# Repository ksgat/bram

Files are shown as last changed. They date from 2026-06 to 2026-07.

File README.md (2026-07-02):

# BRAM!


BRAM is the underactuated, three legged, equilateral triangle from hell.

The project is mostly about control. BRAM’s motion is developed in MuJoCo first, where gait search and reinforcement
learning are used to discover usable crawling and turning behaviors. The current controller combines deterministic
forward/back gait patterns with learned yaw primitives, then blends them into joystick-style movement for the physical
robot.

Right now BRAM can crawl. The next major behavior is self-righting, so the robot can flip itself back over and continue
moving. The goal demo is a side-by-side comparison of the MuJoCo simulation and the real robot crawling, turning, and
eventually recovering from a flip.

## Demo

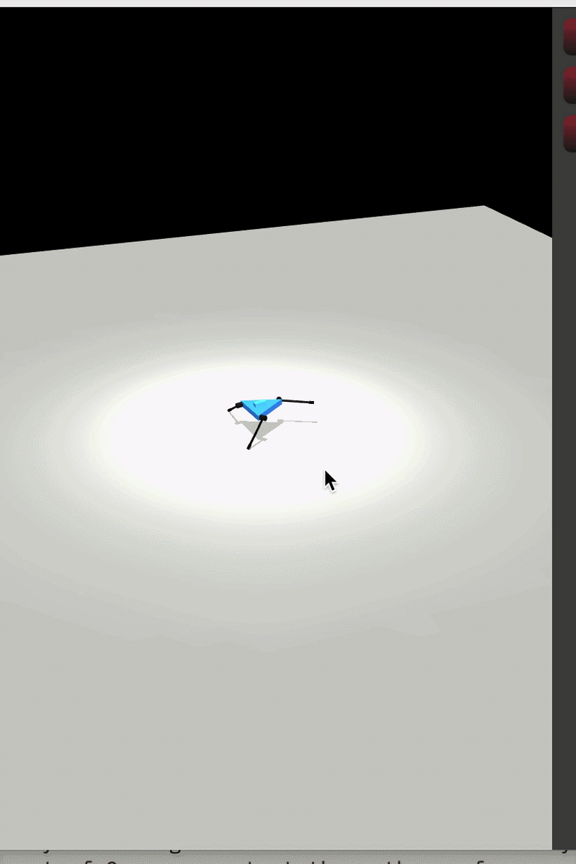
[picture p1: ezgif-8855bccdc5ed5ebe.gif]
BRAM crawling demo


## Project Structure

```text
BRAM
├── CAD/                  # STEP files for the full assembly and major mechanical parts
├── software/             # All robot software
│   ├── firmware/         # ESP32/XIAO firmware for the physical robot
│   └── gait_discovery/   # MuJoCo model, gait search, RL experiments, and controller exports
├── BOM.csv               # Bill of materials with parts, costs, and purchase links
├── JOURNAL.md            # High-level project journal and development summary
└── README.md             # Project overview, wiring notes, BOM table, and documentation
```

# Wiring diagram
Everything is handwired, no pcb.


## Bill of Materials

Source CSV: [BOM.csv](BOM.csv)

| Part | Quantity | Unit Cost | Total Cost | HC Cost | Link |
| --- | ---: | ---: | ---: | ---: | --- |
| 45 kg-cm servo | 3 | $24.99 | $74.97 | $74.97 | [Amazon](https://www.amazon.com/gp/product/B0CNFZ8BW8?smid=A28WSOZPYZ1XET&psc=1) |
| Xiao ESP32C3 | 1 | $10.99 | $10.99 | $10.99 | [Amazon](https://www.amazon.com/gp/product/B0DRNSV5CS?th=1) |
| 3/8 OD carbon rod | 1 | $7.73 | $7.73 | $0.00 | [Windcatcher RC](https://windcatcherrc.com/product/carbon-fiber-tube-10mm-x-8mm-x-1000mm/) |
| BEC | 1 | $8.99 | $8.99 | $8.99 | [Amazon](https://www.amazon.com/gp/product/B0DKTMGBHL?smid=A38CU2XC1RY0BO&psc=1) |
| 9DoF IMU | 1 | $20.49 | $20.49 | $20.49 | [Amazon](https://www.amazon.com/EC-Buying-Accelerometer-Gyroscope-Magnetometer/dp/B0CDGZMLPP) |
| M5 hardware | 1 | $9.99 | $9.99 | $9.99 | [Amazon](https://www.amazon.com/gp/product/B0FG2CT35D?th=1) |
| Ovionic 2S LiPo 1000 mAh | 1 | $23.99 | $23.99 | $23.99 | [Amazon](https://www.amazon.com/gp/product/B07CVBJ3SL?smid=A1KODDOPEPALCP&psc=1) |
| **Total** |  |  | **$157.15** | **$149.42** |  |

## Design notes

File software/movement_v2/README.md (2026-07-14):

# Movement V2

This folder is a BRAM-specific pass at the approach from Inoue et al.,
`Body Design and Gait Generation of Chair-Type Asymmetrical Tripedal Low-rigidity Robot`.

The important idea is not their exact servo angles. Their robot has six servos
and BRAM has three. The useful part to copy is the control structure:

- define a few essential postures
- linearly interpolate between them
- repeat those transitions for walking
- handle self-righting as a separate behavior
- use IMU orientation to decide when to enter or exit recovery

## What Their Repo Actually Has

- `connect_walk.py`: open-loop walking by repeated keyframe interpolation.
- `connect_stand.py` / `connect_once_stand.py`: keyframed stand-up motions.
- `rl_walk.py`: learned ONNX walking policy using IMU quaternion plus recent
  action history.
- `rl_stand.py`: learned ONNX stand-up policy using the same observation style.

They do not have joystick-style walking control. Their walking scripts are
forward-motion behaviors, not full directional teleop controllers.

## BRAM V2 Plan

For BRAM, the practical split should be:

- forward: one PPO-trained specialist primitive
- backward: one separate PPO-trained specialist primitive
- yaw: one PPO-trained yaw-only generalist conditioned on yaw command
- self-righting: separate keyframed recovery first, RL only after hardware
  keyframes exist
- mixed joystick arcs: disabled for demos unless the isolated primitives are
  visually reliable

This intentionally avoids one full joystick policy. Forward/back do not share a
command-conditioned policy, and yaw is the only generalist.

The file `bram_v2_keyframes.json` stores normalized servo commands in BRAM's
servo order:

```text
front, back_left, back_right
```

Values are normalized controller actions in `[-1, 1]`, not microseconds.

## Smoke Test

From the repo root:

```bash
python3 software/movement_v2/keyframe_controller.py \
  --sequence walk_forward \
  --steps 20
```

Backward has a separate seeded sequence:

```bash
python3 software/movement_v2/keyframe_controller.py \
  --sequence walk_backward \
  --steps 20
```

To export a longer command table:

```bash
python3 software/movement_v2/keyframe_controller.py \
  --sequence walk_forward \
  --cycles 10 \
  --csv /tmp/bram_walk_v2.csv
```

Run the MuJoCo primitive smoke suite:

```bash
python3 software/movement_v2/smoke_primitives.py --seconds 4
```

It reports forward/back distance, commanded yaw radians, drift, max tilt, min
chassis height, action delta RMS, and early termination for idle, random-small,
forward, backward, yaw `+1`, yaw `-1`, and half yaw commands.

## Primitive PPO

Use the V2 primitive PPO environment for all three base primitives. The reward
shape follows the paper's walking reward weights:

- progress: `30`
- chassis height: `20`
- upright seat: `5`
- heading/alignment: `2`
- alive: `1`
- death/reset: `-1`
- action delta: `-2`
- hinge velocity: `-2`

BRAM centers the height, upright, and heading/alignment terms at zero and adds a
small active-command stall penalty so standing still does not beat command
progress. The upright term is implemented as a tilt corridor: tilt up to about
`0.45 rad` is allowed because the 1-DOF legs need body rocking, then the penalty
ramps up through about `0.80 rad` and becomes harsher beyond that.

Forward/back specialists use a broad direction reward instead of exact
chassis-axis tracking. Net motion inside a `45 deg` cone gets full progress
credit and fades out by `65 deg`; path waste, wrong-way motion, yaw drift, and
excessive tilt are penalized separately. A slightly skewed but straight,
repeatable crawl is acceptable for the base primitive.

Policy observation:

- previous `4` IMU quaternion frames
- previous `6` normalized servo command frames
- yaw command scalar in `[-1, 1]` for yaw only; forward/back specialists receive
  `0`

Policy output:

- `3` normalized servo targets
- `20 Hz` by default with `--frame-skip 25`
- ESP32 runtime runs the actor online at `20 Hz` and sends normal `50 Hz` PWM
  pulses to the servos

Train the forward specialist:

```bash
.venv-rl/bin/python software/movement_v2/train_primitive_ppo.py \
  --primitive forward \
  --total-steps 300000 \
  --num-envs 4 \
  --episode-seconds 20 \
  --no-randomize-reset \
  --entropy-coef 0.0 \
  --log-std-init -0.8 \
  --hidden-size 128
```

Train the backward specialist separately:

```bash
.venv-rl/bin/python software/movement_v2/train_primitive_ppo.py \
  --primitive backward \
  --total-steps 200000 \
  --num-envs 4 \
  --episode-seconds 8
```

Train the yaw-only generalist:

```bash
.venv-rl/bin/python software/movement_v2/train_primitive_ppo.py \
  --primitive yaw \
  --total-steps 200000 \
  --num-envs 4 \
  --episode-seconds 8
```

Do not enable domain randomization until the nominal primitives move cleanly.
The trainer writes `policy.pt`, `policy_best.pt`, and `metrics.csv` under
`software/movement_v2/runs/rl_primitives/`.

Current corrected-geometry checkpoints use the `15.0 cm` leg endpoint in
`software/gait_discovery/bram.xml`:

- forward: `runs/rl_primitives/forward_primitive_20260706_173603/policy_best.pt`
- backward: `runs/rl_primitives/backward_primitive_20260706_173609/policy_best.pt`
- yaw: `runs/rl_primitives/yaw_primitive_20260706_174051/policy_best.pt`

The forward/back checkpoints are stable 20 second crawl primitives. A free PPO
fine-tune from those seeds was tested and rejected because deterministic eval
collapsed toward stationary behavior; keep the selected `policy_best.pt` files
unless a new run beats them in closed-loop smoke. Yaw was fine-tuned after the
leg-length change and selected with a balanced score over `-1`, `-0.5`, `0.5`,
and `1` yaw commands.

Yaw training now uses a stricter `gait_discovery`-style yaw-in-place eval:
signed yaw progress must be balanced against planar drift throughout the
rollout, action delta, action acceleration, roll/pitch rate, support loss,
contact slip, and chassis height warnings. The per-step yaw reward keeps the
paper's progress/height/up/action/velocity structure, but adds lighter versions
of those yaw-in-place terms so PPO sees the same failure modes without exploding
the value loss.

For the near-term hardware target, yaw drift is gated over time, not only at the
final pose. The current yaw gate is:

- final planar drift `<= 0.040 m`
- mean planar drift `<= 0.025 m`
- max planar drift `<= 0.040 m`
- no termination and no wrong-sign yaw

The base yaw controller should be searched before residual RL. Use the narrow
`yaw_low_drift` search space in `gait_discovery/search_gait.py`; it locks yaw
parameters that do not affect the open-loop CPG, keeps amplitudes/harmonics in a
smooth range, scores against a modest target yaw rate, and hard-gates final,
mean, and max path drift.

Run the base-search plus residual pipeline:

```bash
.venv-rl/bin/python software/movement_v2/run_yaw_base_residual_pipeline.py \
  --directions both \
  --iterations 24 \
  --population 96 \
  --episode-seconds-suite 4,8 \
  --frame-skip 50 \
  --output-hz 40 \
  --residual-steps 50000 \
  --no-randomize-reset
```

For a faster base-only pass:

```bash
.venv-rl/bin/python software/movement_v2/run_yaw_base_residual_pipeline.py \
  --directions both \
  --iterations 8 \
  --population 48 \
  --skip-residual
```

Residual yaw PPO lives in `train_yaw_residual_ppo.py`. It keeps the observation
block from the primitive policies, then appends fixed-base yaw features so the
residual can learn the base phase and timing. The base can be either a JSON
action table or the original searched CPG params; use params when table
resampling changes the contact timing.

- previous `4` IMU quaternion frames
- previous `6` emitted servo actions
- yaw command scalar
- current base action
- previous base action
- base phase `sin/cos`

The actor output is a residual, not a full servo command:

```text
final_action = base_yaw(t, yaw_cmd) + residual_limit * abs(yaw_cmd) * residual
```

Run a 50k residual cutoff test around explicit yaw tables:

```bash
.venv-rl/bin/python software/movement_v2/train_yaw_residual_ppo.py \
  --total-steps 50000 \
  --num-envs 4 \
  --rollout-steps 128 \
  --eval-interval 10 \
  --no-randomize-reset
```

The first 50k residual runs around the old 40 Hz planar yaw tables did **not**
meet the stricter gate. The best observed eval still had zero passing commands;
negative yaw drift stayed above `10 cm`. Treat this as a failed base/curriculum,
not a reason to train the same setup longer.

For a narrower right-yaw test, use direction-specific residual training with a
larger residual and a training-only drift curriculum:

```bash
.venv-rl/bin/python software/movement_v2/train_yaw_residual_ppo.py \
  --train-command yaw_neg1 \
  --eval-suite train \
  --total-steps 50000 \
  --num-envs 4 \
  --rollout-steps 128 \
  --eval-interval 10 \
  --no-randomize-reset \
  --residual-limit 0.35 \
  --start-final-drift-limit-m 0.12 \
  --start-mean-drift-limit-m 0.08 \
  --start-max-drift-limit-m 0.14 \
  --drift-curriculum-steps 50000
```

That run improved the `yaw_neg1` base from about `10.05 cm` final drift /
`13.58 cm` max drift to a best checkpoint around `6.59 cm` final drift /
`10.37 cm` max drift while keeping about `3.09 rad` yaw over `8 s`. It is a real
improvement, but still fails the current path-drift gate. The next thing to improve
is the right-yaw base primitive/search, not another broad residual PPO run.

Current final yaw candidate is packaged in
`software/movement_v2/exports/final_yaw_20260713/manifest.json`:

- full left yaw: `yaw-left_residual_policy_best.pt` on
  `yaw-left_base_params.json`, `2.285 rad`, `0.77 cm` final drift,
  `1.09 cm` mean drift, `1.97 cm` max drift, no termination. This runs at the
  searched CPG's native `10 Hz` hold timing.
- full right yaw: `yaw-right_residual_policy_finetuned_best.pt` on
  `yaw-right_residual_base_table.json`, `2.385 rad`, `0.53 cm` final drift,
  `1.07 cm` mean drift, `2.01 cm` max drift, no termination. This is the
  right-only fine-tuned checkpoint; the previous all-command-selected right
  checkpoint remains in the export package for comparison.
- direct left CPG fallback: `yaw-left_base_params.json`, `2.297 rad`,
  `2.70 cm` final drift, `1.11 cm` mean drift, `3.58 cm` max drift over `8 s`.
- the earlier all-direction residual policy is **not** a passing yaw generalist:
  `yaw_neg1` passed, but half-right and positive yaw did not. Use the
  direction-specific residual checkpoints for full left/right yaw.
- `yaw-left_base_table.json` is not promoted: interpolated table replay changes
  the 10 Hz held CPG contact timing and drifts heavily.

The old `gait_discovery` yaw tables are useful diagnostics, but they are not a
clean teacher on the corrected `15.0 cm` model: full negative yaw can flip sign
and full-rate tables drift heavily. Do not export a new yaw checkpoint unless it
beats the current strict eval and the visual smoke test.

Closed-loop checkpoint smoke test:

```bash
.venv-rl/bin/python software/movement_v2/smoke_policy_primitives.py --seconds 8
.venv-rl/bin/python software/movement_v2/smoke_policy_primitives.py --seconds 20
```

Visualize the same online policies in MuJoCo:

```bash
.venv-rl/bin/python software/movement_v2/visualize_policy_primitives.py --case suite --seconds 8
```

On macOS the script relaunches itself under `mjpython` when opening the viewer.
Use `--case forward`, `--case backward`, `--case yaw_pos`, or `--case yaw_neg`
to inspect one primitive at a time; add `--repeat` to keep looping.

Compare the current yaw actor against the saved degraded yaw actor:

```bash
.venv-rl/bin/python software/movement_v2/visualize_yaw_compare.py --case suite --seconds 8
```

Known corrected-geometry smoke results:

- `8s`: forward `0.1666 m`; backward broad-direction primary `0.0114 m`
  (`x=-0.068 m`, `y=0.125 m`); yaw `+1=2.378 rad`, `-1=1.054 rad`;
  no terminations.
- `20s`: forward `0.5151 m`; backward `0.3886 m`; yaw `+1=2.317 rad`,
  `-1=0.892 rad`; no terminations. Negative yaw drifts more than positive yaw.

## ESP32 Binding

The ESP32 runtime uses a hybrid primitive stack by default:

- forward/back run actor policies online
- yaw uses the base yaw table controller (`kUseBaseControllerForYaw = true`)
- firmware control tick is `25 ms`; yaw table output updates at that tick
- forward/back policy inference is held for two ticks, approximately `20 Hz`

This avoids promoting the 10 Hz yaw PPO fine-tune, which did not beat the
baseline strict eval. The online actor path still maintains the same observation
history as the MuJoCo env:

- previous `4` IMU quaternions, `wxyz`
- previous `6` emitted servo actions
- yaw command scalar for the yaw policy; `0` for forward/back

Export actor weights from the selected checkpoints:

```bash
.venv-rl/bin/python software/movement_v2/export_policy_header.py
```

This writes
`software/firmware/bram_esp32_controller/bram_policy_data.hpp`. The firmware
uses `bram_policy_controller.hpp` for tiny MLP inference and
`kUseOnlinePolicies = true` in
`software/firmware/bram_esp32_controller/bram_esp32_controller.ino`.
Yaw-only commands are routed through `bram_controller.hpp` while
`kUseBaseControllerForYaw` remains enabled.

Optional BNO08x IMU support is behind `BRAM_ENABLE_BNO08X_POLICY_IMU=1`. With
that flag enabled, the firmware reads the BNO080/BNO085 rotation vector as
`w,x,y,z` for the policy. Without it, the policy sees identity quaternion, which
is only useful for compile tests.

Then compile-check firmware:

```bash
arduino-cli compile --fqbn esp32:esp32:XIAO_ESP32C3 \
  software/firmware/bram_esp32_controller
```

## Runtime Arbitration

The ESP32 firmware maps joystick input to primitives with deadbands:

- left stick Y / `f` command: forward/back primitive
- right stick X / `y` command: yaw primitive
- both active: translation priority by default

Set `kBlendMixedCommands = true` in
`software/firmware/bram_esp32_controller/bram_esp32_controller.ino` only after
the isolated forward/back/yaw checks look clean.

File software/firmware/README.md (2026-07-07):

# Bram Firmware

The firmware runs movement_v2 actor policies online. It does not run MuJoCo,
PPO, or Python on-device; it runs exported tiny MLP actor weights from
`bram_esp32_controller/bram_policy_data.hpp` using the IMU quaternion and recent
servo-action history.

Movement V2 defaults to primitive arbitration for demos. If forward/back and yaw are both commanded at the same time, the sketch prioritizes translation and suppresses yaw. Set `kBlendMixedCommands = true` in `bram_esp32_controller/bram_esp32_controller.ino` only after the isolated primitives are reliable enough to re-enable mixed-arc blending.

## Layout

- `bram_esp32_controller/bram_esp32_controller.ino` is the Arduino sketch.
- `bram_esp32_controller/bram_controller.hpp` is the runtime controller logic.
- `bram_esp32_controller/bram_policy_controller.hpp` is the online actor runtime.
- `bram_esp32_controller/bram_policy_data.hpp` is generated actor weight data.
- `bram_esp32_controller/bram_controller_data.hpp` is generated fallback controller data.
- `bno08x_imu_test/bno08x_imu_test.ino` is a standalone BNO080/BNO085 IMU bring-up sketch for a XIAO ESP32-C3 with SDA on `D4` and SCL on `D5`.
- `tools/export_bram_firmware.py` regenerates the data header from a movement_v2 primitive bundle.

## Regenerate Policy Data

From the repo root:

```bash
.venv-rl/bin/python software/movement_v2/export_policy_header.py
```

`kUseOnlinePolicies = true` in the sketch selects this path. The older
`BramController` CPG/table path remains available as a fallback when
`kUseOnlinePolicies` is set to `false`.

## Arduino Dependencies

- ESP32 Arduino core.
- For the IMU test sketch, and for online policy IMU input when
  `BRAM_ENABLE_BNO08X_POLICY_IMU=1`: `Adafruit BNO08x` from Arduino Library Manager.

Native BLE command input is the default Arduino demo path:

```cpp
static constexpr bool kUseSerialInput = false;
```

The XIAO advertises as `BRAM` using a Nordic-UART-style BLE service:

- service UUID: `6e400001-b5a3-f393-e0a9-e50e24dcca9e`
- RX/write UUID: `6e400002-b5a3-f393-e0a9-e50e24dcca9e`
- TX/notify UUID: `6e400003-b5a3-f393-e0a9-e50e24dcca9e`

Send the same ASCII commands over BLE RX:

USB serial override is also enabled by default, so you can still send commands while BLE is compiled in:

```text
f 0.5 y -0.3
0.5 -0.3
stop
```

Set `kUseSerialInput = true` for serial-only bring-up.

The Bluepad32 gamepad hook is left behind `BRAM_ENABLE_BLUEPAD32`, but it is disabled by default. The Arduino Library Manager package named `Bluepad32 for NINA-W10 boards` is for NINA coprocessor boards and does not compile as native ESP32-C3 gamepad input.

## Compile Check

From the repo root:

```bash
arduino-cli compile --fqbn esp32:esp32:XIAO_ESP32C3 software/firmware/bram_esp32_controller
```

IMU test sketch:

```bash
arduino-cli compile --fqbn esp32:esp32:XIAO_ESP32C3 software/firmware/bno08x_imu_test
```

## Safety Notes

- Power servos directly from the 2S battery only if the servos are rated for `8.4 V`.
- Power the ESP32/control electronics from the BEC/regulator, not from the servo rail unless the board regulator supports it.
- Tie battery ground, servo ground, BEC ground, and ESP32 ground together.
- Start with conservative servo pulse limits in the sketch before testing on the robot.
- Bench test with servos disconnected from the mechanism first.

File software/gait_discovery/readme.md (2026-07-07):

3 legged robo

## Setup

```bash
python3 -m venv .venv
source .venv/bin/activate
python -m pip install --upgrade pip
python -m pip install -e .
```

PufferLib currently depends on Torch. If Torch has a wheel for your `python3`,
install the RL stack with:

```bash
python -m pip install -e ".[rl]"
```

For the working RL setup in this directory, use the Python 3.12 venv:

```bash
source .venv-rl/bin/activate
python puffer_smoke.py
```

## Run

Smoke-test the MuJoCo model without opening a window:

```bash
python main.py --headless --seconds 3
```

Open the interactive viewer frozen so you can inspect and tweak the model:

```bash
.venv/bin/mjpython main.py --seconds 0 --pause
```

Run the interactive viewer with a simple sinusoidal starter gait:

```bash
.venv/bin/mjpython main.py
```

Check the Gymnasium environment scaffold that PufferLib can wrap later:

```bash
python main.py --env-check --seconds 3
```

## Movement V2 Training

The current control direction is under `software/movement_v2`: separate
forward/back RL specialist primitives plus a yaw-only command-conditioned RL
generalist. Do not train the old full joystick PPO policy for the base demo.

Train each primitive from the repo root:

```bash
.venv-rl/bin/python software/movement_v2/train_primitive_ppo.py \
  --primitive forward \
  --total-steps 200000 \
  --num-envs 4

.venv-rl/bin/python software/movement_v2/train_primitive_ppo.py \
  --primitive backward \
  --total-steps 200000 \
  --num-envs 4

.venv-rl/bin/python software/movement_v2/train_primitive_ppo.py \
  --primitive yaw \
  --total-steps 200000 \
  --num-envs 4
```

Smoke-test the current primitive controller from the repo root:

```bash
python3 software/movement_v2/smoke_primitives.py --seconds 4
```

The older CAD-mesh attempt is saved as `bram_cad_attempt.xml`. The active
`bram.xml` is a measured hand-written model with a 7.5 inch equilateral
triangle chassis and primitive servo/leg bodies for simulation and RL.

On macOS, MuJoCo's viewer should be launched with:

```bash
.venv/bin/mjpython main.py
```

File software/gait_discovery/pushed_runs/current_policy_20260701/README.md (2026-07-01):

# Bram Current Policy Package - 2026-07-01

This folder is the compact policy snapshot to share/push.

## Reviewable Controller

Current usable policy is the exact component controller:

- forward: deterministic CPG gait in `gaits/forward_best_params.json`
- backward: deterministic CPG gait in `gaits/backward_best_params.json`
- left yaw: exported PPO action table in `yaw_tables/yaw_left_policy_table.json`
- right yaw: exported PPO action table in `yaw_tables/yaw_right_policy_table.json`

Visual review command from repo root:

```bash
.venv-rl/bin/mjpython train_cpg_modulator.py \
  --teacher-controller \
  --forward-gait pushed_runs/current_policy_20260701/gaits/forward_best_params.json \
  --backward-gait pushed_runs/current_policy_20260701/gaits/backward_best_params.json \
  --yaw-left-table pushed_runs/current_policy_20260701/yaw_tables/yaw_left_policy_table.json \
  --yaw-right-table pushed_runs/current_policy_20260701/yaw_tables/yaw_right_policy_table.json \
  --view \
  --view-command primitives \
  --speed 0.8
```

Headless check:

```bash
.venv-rl/bin/python -u train_cpg_modulator.py \
  --teacher-controller \
  --forward-gait pushed_runs/current_policy_20260701/gaits/forward_best_params.json \
  --backward-gait pushed_runs/current_policy_20260701/gaits/backward_best_params.json \
  --yaw-left-table pushed_runs/current_policy_20260701/yaw_tables/yaw_left_policy_table.json \
  --yaw-right-table pushed_runs/current_policy_20260701/yaw_tables/yaw_right_policy_table.json \
  --eval-episodes 1
```

## Status

Primitive commands are reviewable: idle, forward, backward, left yaw, right yaw.

Mixed forward+yaw arcs are not final. Naive blending can terminate or underperform, so do not present that as solved Xbox control yet.

The learned CPG-modulator checkpoint in `experimental_cpg_modulator/` is preserved for reference, but it is not the current best visual policy because it loses too much left-yaw authority.

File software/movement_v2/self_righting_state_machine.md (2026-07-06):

# Self-Righting State Machine Sketch

This is the movement-v2 equivalent of the paper's stand-up split.

The paper's useful pattern:

1. Use IMU quaternion to estimate whether the body is down or upright.
2. If down, run a recovery behavior.
3. If the seat/body becomes upright enough, transition to a normal standing
   posture.
4. Keep stand-up separate from walking.

For BRAM:

```text
state = upright

if up_projection < fallen_threshold:
    state = fallen

fallen:
    choose recovery sequence based on roll/pitch quadrant
    play keyframed kick sequence
    if up_projection > recovered_threshold:
        state = recover_to_neutral

recover_to_neutral:
    interpolate current servo commands to neutral
    state = upright
```

The first real hardware task is not RL. It is to discover three or four
`self_right_*` keyframe sequences by testing the physical robot:

- fallen on left side
- fallen on right side
- upside down / battery-side-up safe case
- awkward partial side case

Once those work manually, an RL policy can be trained around those same motion
families instead of searching from nothing.

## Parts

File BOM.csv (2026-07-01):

Part | Quantity | Unit Cost | Total Cost | HC cost | Links
45 kg-cm servo | 3 | 24.99 | 74.97 | 74.97 | https://www.amazon.com/gp/product/B0CNFZ8BW8?smid=A28WSOZPYZ1XET&psc=1
Xiao ESP32c3 | 1 | 10.99 | 10.99 | 10.99 | https://www.amazon.com/gp/product/B0DRNSV5CS?th=1
3/8 od carbon rod | 1 | 7.73 | 7.73 | 0 | https://windcatcherrc.com/product/carbon-fiber-tube-10mm-x-8mm-x-1000mm/
BEC | 1 | 8.99 | 8.99 | 8.99 | https://www.amazon.com/gp/product/B0DKTMGBHL?smid=A38CU2XC1RY0BO&psc=1
9dof IMU | 1 | 20.49 | 20.49 | 20.49 | https://www.amazon.com/EC-Buying-Accelerometer-Gyroscope-Magnetometer/dp/B0CDGZMLPP
M5 Hardware | 1 | 9.99 | 9.99 | 9.99 | https://www.amazon.com/gp/product/B0FG2CT35D?th=1
Ovionic 2s lipo 1000mah | 1 | 23.99 | 23.99 | 23.99 | https://www.amazon.com/gp/product/B07CVBJ3SL?smid=A1KODDOPEPALCP&psc=1
 |  |  |  | 149.42

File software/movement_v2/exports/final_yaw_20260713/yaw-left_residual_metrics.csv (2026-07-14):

update | global_step | sps | recent_return | recent_yaw | recent_length | eval_reward | eval_score | eval_yaw_distance | eval_planar_drift | eval_mean_planar_drift | eval_max_planar_drift | eval_pass_count | eval_length | policy_loss | value_loss | entropy | approx_kl | yaw_neg1_score | yaw_neg1_yaw_distance | yaw_neg1_target_yaw_distance | yaw_neg1_planar_drift | yaw_neg1_mean_planar_drift | yaw_neg1_max_planar_drift | yaw_neg1_pass_gate | yaw_neg1_length | yaw_neg1_terminated | yaw_neg05_score | yaw_neg05_yaw_distance | yaw_neg05_target_yaw_distance | yaw_neg05_planar_drift | yaw_neg05_mean_planar_drift | yaw_neg05_max_planar_drift | yaw_neg05_pass_gate | yaw_neg05_length | yaw_neg05_terminated | yaw_pos05_score | yaw_pos05_yaw_distance | yaw_pos05_target_yaw_distance | yaw_pos05_planar_drift | yaw_pos05_mean_planar_drift | yaw_pos05_max_planar_drift | yaw_pos05_pass_gate | yaw_pos05_length | yaw_pos05_terminated | yaw_pos1_score | yaw_pos1_yaw_distance | yaw_pos1_target_yaw_distance | yaw_pos1_planar_drift | yaw_pos1_mean_planar_drift | yaw_pos1_max_planar_drift | yaw_pos1_pass_gate | yaw_pos1_length | yaw_pos1_terminated
0 | 0 | 0 | nan | nan | nan | -78.09704811332792 | 8.875966993203743 | 2.297307244669511 | 0.026965498014792772 | 0.011092310719643832 | 0.03581876571649391 | 1 | 80.0 | nan | nan | nan | nan | nan | nan | nan | nan | nan | nan | 0 | 0 | 0 | nan | nan | nan | nan | nan | nan | 0 | 0 | 0 | nan | nan | nan | nan | nan | nan | 0 | 0 | 0 | 8.875966993203743 | 2.297307244669511 | 2.88 | 0.026965498014792772 | 0.011092310719643832 | 0.03581876571649391 | 1 | 80 | 0
1 | 512 | 113 | -215.59188842773438 | 2.056629925966263 | 80.0 | -91.17165140857401 | 8.863121116751898 | 2.276606192984462 | 0.021429484376861468 | 0.01207449133161769 | 0.03288986284346611 | 1 | 80.0 | -0.006232545245438814 | 1188.658447265625 | -1.7429437190294266 | 0.0023840881476644427 | nan | nan | nan | nan | nan | nan | 0 | 0 | 0 | nan | nan | nan | nan | nan | nan | 0 | 0 | 0 | nan | nan | nan | nan | nan | nan | 0 | 0 | 0 | 8.863121116751898 | 2.276606192984462 | 2.88 | 0.021429484376861468 | 0.01207449133161769 | 0.03288986284346611 | 1 | 80 | 0
2 | 1024 | 161 | -285.87597783406574 | 2.0912417074044547 | 80.0 | -125.88445402428233 | 8.490456065211763 | 2.240928957060979 | 0.024670390820816727 | 0.014803712086656567 | 0.03478927111857449 | 1 | 80.0 | -0.0021831186022609472 | 1443.1299743652344 | -1.7423519790172577 | 0.0005918559618294239 | nan | nan | nan | nan | nan | nan | 0 | 0 | 0 | nan | nan | nan | nan | nan | nan | 0 | 0 | 0 | nan | nan | nan | nan | nan | nan | 0 | 0 | 0 | 8.490456065211763 | 2.240928957060979 | 2.88 | 0.024670390820816727 | 0.014803712086656567 | 0.03478927111857449 | 1 | 80 | 0
3 | 1536 | 134 | -268.3898801803589 | 2.095084436237812 | 80.0 | nan | nan | nan | nan | nan | nan | 0 | nan | -9.35759162530303e-05 | 1222.3472137451172 | -1.741686835885048 | 0.000198695546714589 | nan | nan | nan | nan | nan | nan | 0 | 0 | 0 | nan | nan | nan | nan | nan | nan | 0 | 0 | 0 | nan | nan | nan | nan | nan | nan | 0 | 0 | 0 | nan | nan | nan | nan | nan | nan | 0 | 0 | 0
4 | 2048 | 134 | -288.5811055501302 | 2.1124853640794754 | 80.0 | -120.41276054254166 | 4.610916729292138 | 2.3164589277245926 | 0.034980793053208704 | 0.014679767721581827 | 0.044401490344556864 | 0 | 80.0 | -0.00024643843062222004 | 1690.8291778564453 | -1.7414662688970566 | 0.0001916783512569964 | nan | nan | nan | nan | nan | nan | 0 | 0 | 0 | nan | nan | nan | nan | nan | nan | 0 | 0 | 0 | nan | nan | nan | nan | nan | nan | 0 | 0 | 0 | 7.110916729292138 | 2.3164589277245926 | 2.88 | 0.034980793053208704 | 0.014679767721581827 | 0.044401490344556864 | 0 | 80 | 0
5 | 2560 | 149 | -306.94011783599854 | 2.1327952332794666 | 80.0 | nan | nan | nan | nan | nan | nan | 0 | nan | -0.0007851677946746349 | 3420.993438720703 | -1.741483435034752 | 0.000170806422829628 | nan | nan | nan | nan | nan | nan | 0 | 0 | 0 | nan | nan | nan | nan | nan | nan | 0 | 0 | 0 | nan | nan | nan | nan | nan | nan | 0 | 0 | 0 | nan | nan | nan | nan | nan | nan | 0 | 0 | 0
6 | 3072 | 160 | -322.43120744493274 | 2.13493569360839 | 80.0 | -120.43987456281248 | 4.6526114084536765 | 2.3044611638456294 | 0.033731278076758624 | 0.015074912489035835 | 0.04409164144750158 | 0 | 80.0 | -0.0005377861671149731 | 3846.479705810547 | -1.741939589381218 | 0.00018876910326071084 | nan | nan | nan | nan | nan | nan | 0 | 0 | 0 | nan | nan | nan | nan | nan | nan | 0 | 0 | 0 | nan | nan | nan | nan | nan | nan | 0 | 0 | 0 | 7.1526114084536765 | 2.3044611638456294 | 2.88 | 0.033731278076758624 | 0.015074912489035835 | 0.04409164144750158 | 0 | 80 | 0
7 | 3584 | 171 | -322.57157412442297 | 2.132972080599178 | 80.0 | nan | nan | nan | nan | nan | nan | 0 | nan | -0.0012405018787831068 | 1769.1678771972656 | -1.7423667907714844 | 0.00019739862182177603 | nan | nan | nan | nan | nan | nan | 0 | 0 | 0 | nan | nan | nan | nan | nan | nan | 0 | 0 | 0 | nan | nan | nan | nan | nan | nan | 0 | 0 | 0 | nan | nan | nan | nan | nan | nan | 0 | 0 | 0
8 | 4096 | 178 | -320.8567132949829 | 2.1462789848446846 | 80.0 | -107.68187977309302 | 8.936505464135385 | 2.291422643907503 | 0.021455192231240993 | 0.0137942464306352 | 0.03228293064448837 | 1 | 80.0 | -0.0022577412892132998 | 1843.5677947998047 | -1.7425979971885681 | 0.00041416112799197435 | nan | nan | nan | nan | nan | nan | 0 | 0 | 0 | nan | nan | nan | nan | nan | nan | 0 | 0 | 0 | nan | nan | nan | nan | nan | nan | 0 | 0 | 0 | 8.936505464135385 | 2.291422643907503 | 2.88 | 0.021455192231240993 | 0.0137942464306352 | 0.03228293064448837 | 1 | 80 | 0
9 | 4608 | 187 | -319.1342626953125 | 2.155916862487793 | 80.0 | nan | nan | nan | nan | nan | nan | 0 | nan | -0.0013407910009846091 | 761.0855102539062 | -1.7427754998207092 | 0.0008012168982531875 | nan | nan | nan | nan | nan | nan | 0 | 0 | 0 | nan | nan | nan | nan | nan | nan | 0 | 0 | 0 | nan | nan | nan | nan | nan | nan | 0 | 0 | 0 | nan | nan | nan | nan | nan | nan | 0 | 0 | 0
10 | 5120 | 188 | -320.43579467773435 | 2.165974678993225 | 80.0 | -100.35265956054639 | 8.82886450821495 | 2.282308852580516 | 0.020614072309987307 | 0.014099430399416264 | 0.034358447084476905 | 1 | 80.0 | -0.002434961381368339 | 2156.197952270508 | -1.7430506199598312 | 0.0007484124216716737 | nan | nan | nan | nan | nan | nan | 0 | 0 | 0 | nan | nan | nan | nan | nan | nan | 0 | 0 | 0 | nan | nan | nan | nan | nan | nan | 0 | 0 | 0 | 8.82886450821495 | 2.282308852580516 | 2.88 | 0.020614072309987307 | 0.014099430399416264 | 0.034358447084476905 | 1 | 80 | 0
11 | 5632 | 191 | -323.9023434448242 | 2.1666896677017213 | 80.0 | nan | nan | nan | nan | nan | nan | 0 | nan | -0.0023284878116101027 | 952.2683639526367 | -1.743542656302452 | 0.000801826681708917 | nan | nan | nan | nan | nan | nan | 0 | 0 | 0 | nan | nan | nan | nan | nan | nan | 0 | 0 | 0 | nan | nan | nan | nan | nan | nan | 0 | 0 | 0 | nan | nan | nan | nan | nan | nan | 0 | 0 | 0
12 | 6144 | 195 | -295.5328497314453 | 2.1804311943054198 | 80.0 | -87.12478005640234 | 9.339613329288838 | 2.298017162767352 | 0.012128765080281814 | 0.011662179508494573 | 0.024179323276664864 | 1 | 80.0 | -0.0023581632412970066 | 1116.783935546875 | -1.7444330900907516 | 0.0009100497118197381 | nan | nan | nan | nan | nan | nan | 0 | 0 | 0 | nan | nan | nan | nan | nan | nan | 0 | 0 | 0 | nan | nan | nan | nan | nan | nan | 0 | 0 | 0 | 9.339613329288838 | 2.298017162767352 | 2.88 | 0.012128765080281814 | 0.011662179508494573 | 0.024179323276664864 | 1 | 80 | 0
13 | 6656 | 200 | -289.9158367919922 | 2.1742055225372314 | 80.0 | nan | nan | nan | nan | nan | nan | 0 | nan | -0.0040024431655183434 | 1420.642105102539 | -1.7449567466974258 | 0.0011736343149095774 | nan | nan | nan | nan | nan | nan | 0 | 0 | 0 | nan | nan | nan | nan | nan | nan | 0 | 0 | 0 | nan | nan | nan | nan | nan | nan | 0 | 0 | 0 | nan | nan | nan | nan | nan | nan | 0 | 0 | 0
14 | 7168 | 203 | -276.1464279174805 | 2.1651543283462527 | 80.0 | -79.63193378074345 | 9.437222324726761 | 2.2849689903253645 | 0.007728018303852137 | 0.010865370187007672 | 0.01974429430775138 | 1 | 80.0 | -0.0002615319099277258 | 1067.052719116211 | -1.74544657766819 | 0.0008116946555674076 | nan | nan | nan | nan | nan | nan | 0 | 0 | 0 | nan | nan | nan | nan | nan | nan | 0 | 0 | 0 | nan | nan | nan | nan | nan | nan | 0 | 0 | 0 | 9.437222324726761 | 2.2849689903253645 | 2.88 | 0.007728018303852137 | 0.010865370187007672 | 0.01974429430775138 | 1 | 80 | 0
15 | 7680 | 207 | -266.9028775024414 | 2.1699917030334475 | 80.0 | nan | nan | nan | nan | nan | nan | 0 | nan | -0.0010701597202569246 | 1390.4797668457031 | -1.7461276352405548 | 0.00024437750107608736 | nan | nan | nan | nan | nan | nan | 0 | 0 | 0 | nan | nan | nan | nan | nan | nan | 0 | 0 | 0 | nan | nan | nan | nan | nan | nan | 0 | 0 | 0 | nan | nan | nan | nan | nan | nan | 0 | 0 | 0
16 | 8192 | 209 | -267.7662631225586 | 2.1632811880111693 | 80.0 | -103.10875929601954 | 8.806874486102613 | 2.2723394857220907 | 0.024403300441146022 | 0.012087439635926997 | 0.032330651847572535 | 1 | 80.0 | -0.0021599638275802135 | 2004.5359954833984 | -1.7467014789581299 | 0.0008250415557995439 | nan | nan | nan | nan | nan | nan | 0 | 0 | 0 | nan | nan | nan | nan | nan | nan | 0 | 0 | 0 | nan | nan | nan | nan | nan | nan | 0 | 0 | 0 | 8.806874486102613 | 2.2723394857220907 | 2.88 | 0.024403300441146022 | 0.012087439635926997 | 0.032330651847572535 | 1 | 80 | 0
17 | 8704 | 212 | -276.6772448730469 | 2.1660648727416993 | 80.0 | nan | nan | nan | nan | nan | nan | 0 | nan | -0.0030118994181975722 | 1510.5919799804688 | -1.7471470087766647 | 0.0005944909353274852 | nan | nan | nan | nan | nan | nan | 0 | 0 | 0 | nan | nan | nan | nan | nan | nan | 0 | 0 | 0 | nan | nan | nan | nan | nan | nan | 0 | 0 | 0 | nan | nan | nan | nan | nan | nan | 0 | 0 | 0
18 | 9216 | 213 | -269.59364227294924 | 2.157653431892395 | 80.0 | -127.00554058545762 | 8.760962868283372 | 2.28613380883249 | 0.023988046942711602 | 0.01556951472531741 | 0.035325073140174704 | 1 | 80.0 | -0.0015092790126800537 | 818.7760696411133 | -1.7476044595241547 | 0.00042966686305589974 | nan | nan | nan | nan | nan | nan | 0 | 0 | 0 | nan | nan | nan | nan | nan | nan | 0 | 0 | 0 | nan | nan | nan | nan | nan | nan | 0 | 0 | 0 | 8.760962868283372 | 2.28613380883249 | 2.88 | 0.023988046942711602 | 0.01556951472531741 | 0.035325073140174704 | 1 | 80 | 0
19 | 9728 | 217 | -271.63132629394534 | 2.137074987888336 | 80.0 | nan | nan | nan | nan | nan | nan | 0 | nan | -0.002291706157848239 | 987.0267791748047 | -1.7480761408805847 | 0.0008038238156586885 | nan | nan | nan | nan | nan | nan | 0 | 0 | 0 | nan | nan | nan | nan | nan | nan | 0 | 0 | 0 | nan | nan | nan | nan | nan | nan | 0 | 0 | 0 | nan | nan | nan | nan | nan | nan | 0 | 0 | 0
20 | 10240 | 220 | -272.75359924316405 | 2.1426914167404174 | 80.0 | -166.90979273405935 | 4.695495915324231 | 2.267954185433557 | 0.030283947652945165 | 0.020874085179074527 | 0.04314799024079253 | 0 | 80.0 | -0.0012540662719402462 | 1540.7567901611328 | -1.7483916133642197 | 0.000889971706783399 | nan | nan | nan | nan | nan | nan | 0 | 0 | 0 | nan | nan | nan | nan | nan | nan | 0 | 0 | 0 | nan | nan | nan | nan | nan | nan | 0 | 0 | 0 | 7.195495915324231 | 2.267954185433557 | 2.88 | 0.030283947652945165 | 0.020874085179074527 | 0.04314799024079253 | 0 | 80 | 0
21 | 10752 | 225 | -263.28797821044924 | 2.1421982717514036 | 80.0 | nan | nan | nan | nan | nan | nan | 0 | nan | -0.0015402310527861118 | 645.6778259277344 | -1.74872887134552 | 0.00040574491140432656 | nan | nan | nan | nan | nan | nan | 0 | 0 | 0 | nan | nan | nan | nan | nan | nan | 0 | 0 | 0 | nan | nan | nan | nan | nan | nan | 0 | 0 | 0 | nan | nan | nan | nan | nan | nan | 0 | 0 | 0
22 | 11264 | 227 | -262.37170562744143 | 2.143997001647949 | 80.0 | -96.4414676599093 | 8.404166073944149 | 2.2316835611774364 | 0.028872601691001674 | 0.01225708752521146 | 0.03527384658654585 | 1 | 80.0 | -0.0011414227774366736 | 929.2920303344727 | -1.7488564997911453 | 0.0004748171486426145 | nan | nan | nan | nan | nan | nan | 0 | 0 | 0 | nan | nan | nan | nan | nan | nan | 0 | 0 | 0 | nan | nan | nan | nan | nan | nan | 0 | 0 | 0 | 8.404166073944149 | 2.2316835611774364 | 2.88 | 0.028872601691001674 | 0.01225708752521146 | 0.03527384658654585 | 1 | 80 | 0
23 | 11776 | 231 | -271.01082427978514 | 2.1241167688369753 | 80.0 | nan | nan | nan | nan | nan | nan | 0 | nan | -0.0009474039543420076 | 2235.292022705078 | -1.7487842738628387 | 0.0005351805011741817 | nan | nan | nan | nan | nan | nan | 0 | 0 | 0 | nan | nan | nan | nan | nan | nan | 0 | 0 | 0 | nan | nan | nan | nan | nan | nan | 0 | 0 | 0 | nan | nan | nan | nan | nan | nan | 0 | 0 | 0
24 | 12288 | 233 | -258.1648049926758 | 2.1325091195106505 | 80.0 | -79.47524758470921 | 8.767814654925802 | 2.231439030125139 | 0.01983497332444898 | 0.009603146122758123 | 0.02708923793598895 | 1 | 80.0 | -0.0014599787537008524 | 444.45567321777344 | -1.7484618872404099 | 0.0004370755923446268 | nan | nan | nan | nan | nan | nan | 0 | 0 | 0 | nan | nan | nan | nan | nan | nan | 0 | 0 | 0 | nan | nan | nan | nan | nan | nan | 0 | 0 | 0 | 8.767814654925802 | 2.231439030125139 | 2.88 | 0.01983497332444898 | 0.009603146122758123 | 0.02708923793598895 | 1 | 80 | 0
25 | 12800 | 236 | -245.10702392578125 | 2.1343492388725283 | 80.0 | nan | nan | nan | nan | nan | nan | 0 | nan | -0.0021292422607075423 | 920.6499633789062 | -1.748024806380272 | 0.0008261803886853158 | nan | nan | nan | nan | nan | nan | 0 | 0 | 0 | nan | nan | nan | nan | nan | nan | 0 | 0 | 0 | nan | nan | nan | nan | nan | nan | 0 | 0 | 0 | nan | nan | nan | nan | nan | nan | 0 | 0 | 0
26 | 13312 | 238 | -254.84767791748047 | 2.139894070625305 | 80.0 | -87.99239714802808 | 8.466185835168282 | 2.210131020510794 | 0.02288907187016557 | 0.010233567177305787 | 0.03150732454617612 | 1 | 80.0 | -0.00014421611558645964 | 2069.5587005615234 | -1.7479811310768127 | 0.000597219419432804 | nan | nan | nan | nan | nan | nan | 0 | 0 | 0 | nan | nan | nan | nan | nan | nan | 0 | 0 | 0 | nan | nan | nan | nan | nan | nan | 0 | 0 | 0 | 8.466185835168282 | 2.210131020510794 | 2.88 | 0.02288907187016557 | 0.010233567177305787 | 0.03150732454617612 | 1 | 80 | 0
27 | 13824 | 241 | -261.53398193359374 | 2.141196961402893 | 80.0 | nan | nan | nan | nan | nan | nan | 0 | nan | -0.0022259445395320654 | 1460.4608459472656 | -1.7481644749641418 | 0.0002528903423808515 | nan | nan | nan | nan | nan | nan | 0 | 0 | 0 | nan | nan | nan | nan | nan | nan | 0 | 0 | 0 | nan | nan | nan | nan | nan | nan | 0 | 0 | 0 | nan | nan | nan | nan | nan | nan | 0 | 0 | 0
28 | 14336 | 243 | -254.70801879882814 | 2.1303604865074157 | 80.0 | -74.578917752142 | 8.896867525395253 | 2.236228518132454 | 0.01755012080308042 | 0.009816483154345457 | 0.024186193631535444 | 1 | 80.0 | -0.00046801171265542507 | 941.3096084594727 | -1.7479517757892609 | 0.0003842526348307729 | nan | nan | nan | nan | nan | nan | 0 | 0 | 0 | nan | nan | nan | nan | nan | nan | 0 | 0 | 0 | nan | nan | nan | nan | nan | nan | 0 | 0 | 0 | 8.896867525395253 | 2.236228518132454 | 2.88 | 0.01755012080308042 | 0.009816483154345457 | 0.024186193631535444 | 1 | 80 | 0
29 | 14848 | 246 | -258.69297668457034 | 2.141341016292572 | 80.0 | nan | nan | nan | nan | nan | nan | 0 | nan | -0.002485688077285886 | 776.7536087036133 | -1.7475836426019669 | 0.00034168281126767397 | nan | nan | nan | nan | nan | nan | 0 | 0 | 0 | nan | nan | nan | nan | nan | nan | 0 | 0 | 0 | nan | nan | nan | nan | nan | nan | 0 | 0 | 0 | nan | nan | nan | nan | nan | nan | 0 | 0 | 0
30 | 15360 | 248 | -246.31579376220702 | 2.1577423548698427 | 80.0 | -101.74737299308393 | 8.912648950760687 | 2.2703424782571524 | 0.021058881911607263 | 0.012173823702564769 | 0.028879817399171514 | 1 | 80.0 | -0.001817677984945476 | 708.8396530151367 | -1.7472121566534042 | 0.000576953956624493 | nan | nan | nan | nan | nan | nan | 0 | 0 | 0 | nan | nan | nan | nan | nan | nan | 0 | 0 | 0 | nan | nan | nan | nan | nan | nan | 0 | 0 | 0 | 8.912648950760687 | 2.2703424782571524 | 2.88 | 0.021058881911607263 | 0.012173823702564769 | 0.028879817399171514 | 1 | 80 | 0
31 | 15872 | 251 | -251.8419125366211 | 2.1538077998161316 | 80.0 | nan | nan | nan | nan | nan | nan | 0 | nan | 1.2498348951339722e-05 | 1601.965805053711 | -1.7465173453092575 | 0.00023732412955723703 | nan | nan | nan | nan | nan | nan | 0 | 0 | 0 | nan | nan | nan | nan | nan | nan | 0 | 0 | 0 | nan | nan | nan | nan | nan | nan | 0 | 0 | 0 | nan | nan | nan | nan | nan | nan | 0 | 0 | 0
32 | 16384 | 251 | -264.41684295654295 | 2.1492989587783815 | 80.0 | -112.21051639432689 | 8.679629347440697 | 2.265683312740272 | 0.026190903901899324 | 0.014038658461314218 | 0.03296784114006136 | 1 | 80.0 | -0.001950006582774222 | 1012.5821838378906 | -1.7461006492376328 | 0.00024356044013984501 | nan | nan | nan | nan | nan | nan | 0 | 0 | 0 | nan | nan | nan | nan | nan | nan | 0 | 0 | 0 | nan | nan | nan | nan | nan | nan | 0 | 0 | 0 | 8.679629347440697 | 2.265683312740272 | 2.88 | 0.026190903901899324 | 0.014038658461314218 | 0.03296784114006136 | 1 | 80 | 0
33 | 16896 | 247 | -263.73787475585937 | 2.144003219604492 | 80.0 | nan | nan | nan | nan | nan | nan | 0 | nan | -0.002086657186737284 | 1035.2126922607422 | -1.7458926439285278 | 0.0006544537609443069 | nan | nan | nan | nan | nan | nan | 0 | 0 | 0 | nan | nan | nan | nan | nan | nan | 0 | 0 | 0 | nan | nan | nan | nan | nan | nan | 0 | 0 | 0 | nan | nan | nan | nan | nan | nan | 0 | 0 | 0
34 | 17408 | 248 | -262.5594818115234 | 2.14633594751358 | 80.0 | -81.15849393293591 | 8.895698554023454 | 2.273558647122409 | 0.022768680928278693 | 0.01098631982965547 | 0.03034012088366003 | 1 | 80.0 | -0.001631910097785294 | 1140.5063171386719 | -1.7464351058006287 | 0.0007711016514804214 | nan | nan | nan | nan | nan | nan | 0 | 0 | 0 | nan | nan | nan | nan | nan | nan | 0 | 0 | 0 | nan | nan | nan | nan | nan | nan | 0 | 0 | 0 | 8.895698554023454 | 2.273558647122409 | 2.88 | 0.022768680928278693 | 0.01098631982965547 | 0.03034012088366003 | 1 | 80 | 0
35 | 17920 | 249 | -263.23691192626956 | 2.155202739238739 | 80.0 | nan | nan | nan | nan | nan | nan | 0 | nan | -1.2903474271297455e-06 | 1729.9297332763672 | -1.746952936053276 | 0.0003810627677012235 | nan | nan | nan | nan | nan | nan | 0 | 0 | 0 | nan | nan | nan | nan | nan | nan | 0 | 0 | 0 | nan | nan | nan | nan | nan | nan | 0 | 0 | 0 | nan | nan | nan | nan | nan | nan | 0 | 0 | 0
36 | 18432 | 250 | -268.29838592529296 | 2.136159281730652 | 80.0 | -112.94583568653093 | 8.388967714888041 | 2.2077495628046018 | 0.022212818226969477 | 0.013736634256912291 | 0.03170414912685038 | 1 | 80.0 | -0.002787067089229822 | 1317.9404602050781 | -1.7473352998495102 | 0.00041086997953243554 | nan | nan | nan | nan | nan | nan | 0 | 0 | 0 | nan | nan | nan | nan | nan | nan | 0 | 0 | 0 | nan | nan | nan | nan | nan | nan | 0 | 0 | 0 | 8.388967714888041 | 2.2077495628046018 | 2.88 | 0.022212818226969477 | 0.013736634256912291 | 0.03170414912685038 | 1 | 80 | 0
37 | 18944 | 252 | -274.9182711791992 | 2.116334466934204 | 80.0 | nan | nan | nan | nan | nan | nan | 0 | nan | -0.0007475384045392275 | 1373.4390258789062 | -1.747769057750702 | 0.00040591671131551266 | nan | nan | nan | nan | nan | nan | 0 | 0 | 0 | nan | nan | nan | nan | nan | nan | 0 | 0 | 0 | nan | nan | nan | nan | nan | nan | 0 | 0 | 0 | nan | nan | nan | nan | nan | nan | 0 | 0 | 0
38 | 19456 | 253 | -276.35936584472654 | 2.123756136894226 | 80.0 | -89.38256157879393 | 8.886463314970836 | 2.2102670559259336 | 0.004367043025384924 | 0.00959014429483258 | 0.02431861738324158 | 1 | 80.0 | -0.001802176469936967 | 1245.2501068115234 | -1.748072475194931 | 0.00037065494689159095 | nan | nan | nan | nan | nan | nan | 0 | 0 | 0 | nan | nan | nan | nan | nan | nan | 0 | 0 | 0 | nan | nan | nan | nan | nan | nan | 0 | 0 | 0 | 8.886463314970836 | 2.2102670559259336 | 2.88 | 0.004367043025384924 | 0.00959014429483258 | 0.02431861738324158 | 1 | 80 | 0
39 | 19968 | 255 | -271.2808938598633 | 2.1077062249183656 | 80.0 | nan | nan | nan | nan | nan | nan | 0 | nan | -0.00198587728664279 | 584.6650466918945 | -1.748013198375702 | 0.0005847897264175117 | nan | nan | nan | nan | nan | nan | 0 | 0 | 0 | nan | nan | nan | nan | nan | nan | 0 | 0 | 0 | nan | nan | nan | nan | nan | nan | 0 | 0 | 0 | nan | nan | nan | nan | nan | nan | 0 | 0 | 0
40 | 20480 | 253 | -264.2718881225586 | 2.1243753099441527 | 80.0 | -104.81937284365871 | 8.522123986872597 | 2.26641110969453 | 0.028748194600672416 | 0.013595632194328449 | 0.038211963793852444 | 1 | 80.0 | -0.0025262412091251463 | 581.6955642700195 | -1.7484685629606247 | 0.0008371963340323418 | nan | nan | nan | nan | nan | nan | 0 | 0 | 0 | nan | nan | nan | nan | nan | nan | 0 | 0 | 0 | nan | nan | nan | nan | nan | nan | 0 | 0 | 0 | 8.522123986872597 | 2.26641110969453 | 2.88 | 0.028748194600672416 | 0.013595632194328449 | 0.038211963793852444 | 1 | 80 | 0
41 | 20992 | 253 | -259.537966003418 | 2.133078541755676 | 80.0 | nan | nan | nan | nan | nan | nan | 0 | nan | -0.0036134475958533585 | 843.4213638305664 | -1.7489170581102371 | 0.0007698094414081424 | nan | nan | nan | nan | nan | nan | 0 | 0 | 0 | nan | nan | nan | nan | nan | nan | 0 | 0 | 0 | nan | nan | nan | nan | nan | nan | 0 | 0 | 0 | nan | nan | nan | nan | nan | nan | 0 | 0 | 0
42 | 21504 | 237 | -250.15000762939454 | 2.1323713660240173 | 80.0 | -115.93945557720922 | 8.679621724370842 | 2.2520942053209567 | 0.022949358079805388 | 0.013215249535216361 | 0.03135706648810333 | 1 | 80.0 | -0.0012368735624477267 | 597.8145751953125 | -1.7501459419727325 | 0.0008800188661552966 | nan | nan | nan | nan | nan | nan | 0 | 0 | 0 | nan | nan | nan | nan | nan | nan | 0 | 0 | 0 | nan | nan | nan | nan | nan | nan | 0 | 0 | 0 | 8.679621724370842 | 2.2520942053209567 | 2.88 | 0.022949358079805388 | 0.013215249535216361 | 0.03135706648810333 | 1 | 80 | 0
43 | 22016 | 229 | -254.22915710449217 | 2.132964951992035 | 80.0 | nan | nan | nan | nan | nan | nan | 0 | nan | -0.0017283884808421135 | 1202.7662811279297 | -1.751549482345581 | 0.0003397757245693356 | nan | nan | nan | nan | nan | nan | 0 | 0 | 0 | nan | nan | nan | nan | nan | nan | 0 | 0 | 0 | nan | nan | nan | nan | nan | nan | 0 | 0 | 0 | nan | nan | nan | nan | nan | nan | 0 | 0 | 0
44 | 22528 | 223 | -239.9172348022461 | 2.1376422905921935 | 80.0 | -108.70430342232575 | 8.233283189666727 | 2.2380165128182616 | 0.03331731901592684 | 0.01587679301537196 | 0.03833789549961514 | 1 | 80.0 | -0.0019138297066092491 | 581.3362197875977 | -1.7522565126419067 | 0.0005139279237482697 | nan | nan | nan | nan | nan | nan | 0 | 0 | 0 | nan | nan | nan | nan | nan | nan | 0 | 0 | 0 | nan | nan | nan | nan | nan | nan | 0 | 0 | 0 | 8.233283189666727 | 2.2380165128182616 | 2.88 | 0.03331731901592684 | 0.01587679301537196 | 0.03833789549961514 | 1 | 80 | 0
45 | 23040 | 218 | -238.1605844116211 | 2.1331862926483156 | 80.0 | nan | nan | nan | nan | nan | nan | 0 | nan | -0.0017866564448922873 | 1562.0715637207031 | -1.7523083984851837 | 0.0008080561528913677 | nan | nan | nan | nan | nan | nan | 0 | 0 | 0 | nan | nan | nan | nan | nan | nan | 0 | 0 | 0 | nan | nan | nan | nan | nan | nan | 0 | 0 | 0 | nan | nan | nan | nan | nan | nan | 0 | 0 | 0
46 | 23552 | 214 | -236.57261505126954 | 2.1287417078018187 | 80.0 | -102.79897845436125 | 8.666865968406308 | 2.2380540579957278 | 0.022639314852913827 | 0.014271582609841488 | 0.02761137028764622 | 1 | 80.0 | -0.001372721279039979 | 706.11962890625 | -1.7521309852600098 | 0.0004990538000129163 | nan | nan | nan | nan | nan | nan | 0 | 0 | 0 | nan | nan | nan | nan | nan | nan | 0 | 0 | 0 | nan | nan | nan | nan | nan | nan | 0 | 0 | 0 | 8.666865968406308 | 2.2380540579957278 | 2.88 | 0.022639314852913827 | 0.014271582609841488 | 0.02761137028764622 | 1 | 80 | 0
47 | 24064 | 210 | -247.68726684570314 | 2.113769793510437 | 80.0 | nan | nan | nan | nan | nan | nan | 0 | nan | -0.00027832225896418095 | 1962.0174102783203 | -1.7521099299192429 | 0.0002485475561115891 | nan | nan | nan | nan | nan | nan | 0 | 0 | 0 | nan | nan | nan | nan | nan | nan | 0 | 0 | 0 | nan | nan | nan | nan | nan | nan | 0 | 0 | 0 | nan | nan | nan | nan | nan | nan | 0 | 0 | 0
48 | 24576 | 206 | -249.1700503540039 | 2.1114171743392944 | 80.0 | -98.09174896792506 | 8.491115974010112 | 2.2264821804914323 | 0.025689591813012422 | 0.01233871545851092 | 0.03136658467422501 | 1 | 80.0 | 0.0003288990119472146 | 952.6786117553711 | -1.7522832453250885 | 0.0001397289743181318 | nan | nan | nan | nan | nan | nan | 0 | 0 | 0 | nan | nan | nan | nan | nan | nan | 0 | 0 | 0 | nan | nan | nan | nan | nan | nan | 0 | 0 | 0 | 8.491115974010112 | 2.2264821804914323 | 2.88 | 0.025689591813012422 | 0.01233871545851092 | 0.03136658467422501 | 1 | 80 | 0
49 | 25088 | 202 | -250.04284057617187 | 2.0998774409294128 | 80.0 | nan | nan | nan | nan | nan | nan | 0 | nan | -0.0014213051181286573 | 533.0351181030273 | -1.752841755747795 | 0.0002576551341917366 | nan | nan | nan | nan | nan | nan | 0 | 0 | 0 | nan | nan | nan | nan | nan | nan | 0 | 0 | 0 | nan | nan | nan | nan | nan | nan | 0 | 0 | 0 | nan | nan | nan | nan | nan | nan | 0 | 0 | 0
50 | 25600 | 199 | -253.35286834716797 | 2.091661388874054 | 80.0 | -107.75712104358117 | 8.189881921152853 | 2.189721482397374 | 0.026477320658191958 | 0.014280962828791637 | 0.03213275527625533 | 1 | 80.0 | -0.0006557716988027096 | 989.2709350585938 | -1.7541067898273468 | 0.00027406387380324304 | nan | nan | nan | nan | nan | nan | 0 | 0 | 0 | nan | nan | nan | nan | nan | nan | 0 | 0 | 0 | nan | nan | nan | nan | nan | nan | 0 | 0 | 0 | 8.189881921152853 | 2.189721482397374 | 2.88 | 0.026477320658191958 | 0.014280962828791637 | 0.03213275527625533 | 1 | 80 | 0
51 | 26112 | 195 | -247.77678588867187 | 2.0916971349716187 | 80.0 | nan | nan | nan | nan | nan | nan | 0 | nan | -0.00428702961653471 | 523.1599235534668 | -1.7550528943538666 | 0.0007495069585274905 | nan | nan | nan | nan | nan | nan | 0 | 0 | 0 | nan | nan | nan | nan | nan | nan | 0 | 0 | 0 | nan | nan | nan | nan | nan | nan | 0 | 0 | 0 | nan | nan | nan | nan | nan | nan | 0 | 0 | 0
52 | 26624 | 193 | -244.8599188232422 | 2.083521206378937 | 80.0 | -85.47719414154203 | 8.88281414577951 | 2.2447701543167478 | 0.015829900557405508 | 0.010408124809658723 | 0.026800216877617026 | 1 | 80.0 | -0.0013770351652055979 | 615.7080688476562 | -1.7557581663131714 | 0.0022337498667184263 | nan | nan | nan | nan | nan | nan | 0 | 0 | 0 | nan | nan | nan | nan | nan | nan | 0 | 0 | 0 | nan | nan | nan | nan | nan | nan | 0 | 0 | 0 | 8.88281414577951 | 2.2447701543167478 | 2.88 | 0.015829900557405508 | 0.010408124809658723 | 0.026800216877617026 | 1 | 80 | 0
53 | 27136 | 191 | -240.38155151367187 | 2.075033061504364 | 80.0 | nan | nan | nan | nan | nan | nan | 0 | nan | -0.0009733082260936499 | 1024.1438598632812 | -1.7563122808933258 | 0.0005309155967552215 | nan | nan | nan | nan | nan | nan | 0 | 0 | 0 | nan | nan | nan | nan | nan | nan | 0 | 0 | 0 | nan | nan | nan | nan | nan | nan | 0 | 0 | 0 | nan | nan | nan | nan | nan | nan | 0 | 0 | 0
54 | 27648 | 188 | -233.491318359375 | 2.0753982305526733 | 80.0 | -86.53821221828004 | 8.414761889863689 | 2.147124831727898 | 0.014769455101123083 | 0.009150059934436652 | 0.021719849939166348 | 1 | 80.0 | -0.0029015449108555913 | 563.4128570556641 | -1.7570668309926987 | 0.0007296819530893117 | nan | nan | nan | nan | nan | nan | 0 | 0 | 0 | nan | nan | nan | nan | nan | nan | 0 | 0 | 0 | nan | nan | nan | nan | nan | nan | 0 | 0 | 0 | 8.414761889863689 | 2.147124831727898 | 2.88 | 0.014769455101123083 | 0.009150059934436652 | 0.021719849939166348 | 1 | 80 | 0
55 | 28160 | 186 | -237.35251068115235 | 2.0802921795845033 | 80.0 | nan | nan | nan | nan | nan | nan | 0 | nan | 0.0002192577812820673 | 1761.7575378417969 | -1.7580234855413437 | 0.0004747211351059377 | nan | nan | nan | nan | nan | nan | 0 | 0 | 0 | nan | nan | nan | nan | nan | nan | 0 | 0 | 0 | nan | nan | nan | nan | nan | nan | 0 | 0 | 0 | nan | nan | nan | nan | nan | nan | 0 | 0 | 0
56 | 28672 | 184 | -233.22103393554687 | 2.0716733288764955 | 80.0 | -95.87229069395735 | 8.78797870282067 | 2.204020743519029 | 0.015277853755533819 | 0.010663150216986928 | 0.020279327738705766 | 1 | 80.0 | -0.00148129859007895 | 537.1543579101562 | -1.758337363600731 | 0.00044092515599913895 | nan | nan | nan | nan | nan | nan | 0 | 0 | 0 | nan | nan | nan | nan | nan | nan | 0 | 0 | 0 | nan | nan | nan | nan | nan | nan | 0 | 0 | 0 | 8.78797870282067 | 2.204020743519029 | 2.88 | 0.015277853755533819 | 0.010663150216986928 | 0.020279327738705766 | 1 | 80 | 0
57 | 29184 | 182 | -237.1109649658203 | 2.071214756965637 | 80.0 | nan | nan | nan | nan | nan | nan | 0 | nan | -0.0016842442564666271 | 788.2808151245117 | -1.7583858668804169 | 0.0003104983188677579 | nan | nan | nan | nan | nan | nan | 0 | 0 | 0 | nan | nan | nan | nan | nan | nan | 0 | 0 | 0 | nan | nan | nan | nan | nan | nan | 0 | 0 | 0 | nan | nan | nan | nan | nan | nan | 0 | 0 | 0
58 | 29696 | 179 | -235.9234161376953 | 2.0686246728897095 | 80.0 | -87.74541151211663 | 8.586768637209307 | 2.1769769585627343 | 0.014886799077366572 | 0.010156963649207661 | 0.02180545972871204 | 1 | 80.0 | -0.0011400670045986772 | 631.8623275756836 | -1.7591496258974075 | 0.0006457404815591872 | nan | nan | nan | nan | nan | nan | 0 | 0 | 0 | nan | nan | nan | nan | nan | nan | 0 | 0 | 0 | nan | nan | nan | nan | nan | nan | 0 | 0 | 0 | 8.586768637209307 | 2.1769769585627343 | 2.88 | 0.014886799077366572 | 0.010156963649207661 | 0.02180545972871204 | 1 | 80 | 0
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

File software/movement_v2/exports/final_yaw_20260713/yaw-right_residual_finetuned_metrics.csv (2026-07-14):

update | global_step | sps | recent_return | recent_yaw | recent_length | eval_reward | eval_score | eval_yaw_distance | eval_planar_drift | eval_mean_planar_drift | eval_max_planar_drift | eval_pass_count | eval_length | policy_loss | value_loss | entropy | approx_kl | yaw_neg1_score | yaw_neg1_yaw_distance | yaw_neg1_target_yaw_distance | yaw_neg1_planar_drift | yaw_neg1_mean_planar_drift | yaw_neg1_max_planar_drift | yaw_neg1_pass_gate | yaw_neg1_length | yaw_neg1_terminated | yaw_neg05_score | yaw_neg05_yaw_distance | yaw_neg05_target_yaw_distance | yaw_neg05_planar_drift | yaw_neg05_mean_planar_drift | yaw_neg05_max_planar_drift | yaw_neg05_pass_gate | yaw_neg05_length | yaw_neg05_terminated | yaw_pos05_score | yaw_pos05_yaw_distance | yaw_pos05_target_yaw_distance | yaw_pos05_planar_drift | yaw_pos05_mean_planar_drift | yaw_pos05_max_planar_drift | yaw_pos05_pass_gate | yaw_pos05_length | yaw_pos05_terminated | yaw_pos1_score | yaw_pos1_yaw_distance | yaw_pos1_target_yaw_distance | yaw_pos1_planar_drift | yaw_pos1_mean_planar_drift | yaw_pos1_max_planar_drift | yaw_pos1_pass_gate | yaw_pos1_length | yaw_pos1_terminated
0 | 0 | 0 | nan | nan | nan | -1815.8822657888493 | 4.616139278879288 | 2.34082054339191 | 0.016312667234419154 | 0.01399095776991733 | 0.02789422188759939 | 0 | 400.0 | nan | nan | nan | nan | 7.116139278879288 | 2.34082054339191 | 2.88 | 0.016312667234419154 | 0.01399095776991733 | 0.02789422188759939 | 0 | 400 | 0 | nan | nan | nan | nan | nan | nan | 0 | 0 | 0 | nan | nan | nan | nan | nan | nan | 0 | 0 | 0 | nan | nan | nan | nan | nan | nan | 0 | 0 | 0
1 | 512 | 296 | nan | nan | nan | -1839.0876060432342 | 6.442087040746742 | 2.3891201612476363 | 0.005749366998182044 | 0.013225015429385017 | 0.02469125952850276 | 0 | 400.0 | -0.0034996180329471827 | 3484.7762756347656 | -1.7578332126140594 | 0.00035677175037562847 | 8.942087040746742 | 2.3891201612476363 | 2.88 | 0.005749366998182044 | 0.013225015429385017 | 0.02469125952850276 | 0 | 400 | 0 | nan | nan | nan | nan | nan | nan | 0 | 0 | 0 | nan | nan | nan | nan | nan | nan | 0 | 0 | 0 | nan | nan | nan | nan | nan | nan | 0 | 0 | 0
2 | 1024 | 315 | nan | nan | nan | -2503.2974634617735 | 1.4652709139328253 | 2.2598385644260635 | 0.020190417652484336 | 0.016915244423291495 | 0.03262288022174344 | 0 | 400.0 | -0.0005600954173132777 | 8688.955688476562 | -1.757502794265747 | 0.00018251704750582576 | 3.9652709139328253 | 2.2598385644260635 | 2.88 | 0.020190417652484336 | 0.016915244423291495 | 0.03262288022174344 | 0 | 400 | 0 | nan | nan | nan | nan | nan | nan | 0 | 0 | 0 | nan | nan | nan | nan | nan | nan | 0 | 0 | 0 | nan | nan | nan | nan | nan | nan | 0 | 0 | 0
3 | 1536 | 371 | nan | nan | nan | nan | nan | nan | nan | nan | nan | 0 | nan | -0.00044953334145247936 | 14218.344116210938 | -1.7571895122528076 | 7.669863407500088e-05 | nan | nan | nan | nan | nan | nan | 0 | 0 | 0 | nan | nan | nan | nan | nan | nan | 0 | 0 | 0 | nan | nan | nan | nan | nan | nan | 0 | 0 | 0 | nan | nan | nan | nan | nan | nan | 0 | 0 | 0
4 | 2048 | 362 | -3407.9281005859375 | 1.9779932796955109 | 400.0 | -1735.8205714593269 | 3.84867324599435 | 2.4145807933061096 | 0.02422403968191197 | 0.013872974567103352 | 0.029053883736012472 | 0 | 400.0 | -0.00160876102745533 | 4144.187103271484 | -1.757195234298706 | 0.00011963199358433485 | 6.34867324599435 | 2.4145807933061096 | 2.88 | 0.02422403968191197 | 0.013872974567103352 | 0.029053883736012472 | 0 | 400 | 0 | nan | nan | nan | nan | nan | nan | 0 | 0 | 0 | nan | nan | nan | nan | nan | nan | 0 | 0 | 0 | nan | nan | nan | nan | nan | nan | 0 | 0 | 0
5 | 2560 | 389 | -3407.9281005859375 | 1.9779932796955109 | 400.0 | nan | nan | nan | nan | nan | nan | 0 | nan | -7.703190203756094e-05 | 12255.81201171875 | -1.7574357688426971 | 0.00011496760998852551 | nan | nan | nan | nan | nan | nan | 0 | 0 | 0 | nan | nan | nan | nan | nan | nan | 0 | 0 | 0 | nan | nan | nan | nan | nan | nan | 0 | 0 | 0 | nan | nan | nan | nan | nan | nan | 0 | 0 | 0
6 | 3072 | 301 | -3407.9281005859375 | 1.9779932796955109 | 400.0 | -1959.7717121186943 | 4.439397074591072 | 2.2819644467549898 | 0.006768021830763357 | 0.01425297373529988 | 0.02744605729771067 | 0 | 400.0 | -0.000597409438341856 | 17705.1376953125 | -1.7574322819709778 | 6.094737909734249e-05 | 6.939397074591072 | 2.2819644467549898 | 2.88 | 0.006768021830763357 | 0.01425297373529988 | 0.02744605729771067 | 0 | 400 | 0 | nan | nan | nan | nan | nan | nan | 0 | 0 | 0 | nan | nan | nan | nan | nan | nan | 0 | 0 | 0 | nan | nan | nan | nan | nan | nan | 0 | 0 | 0
7 | 3584 | 288 | -3584.9049377441406 | 1.9639501422643661 | 400.0 | nan | nan | nan | nan | nan | nan | 0 | nan | -0.0012779831886291504 | 5601.2867431640625 | -1.7573905289173126 | 0.00011831711162813008 | nan | nan | nan | nan | nan | nan | 0 | 0 | 0 | nan | nan | nan | nan | nan | nan | 0 | 0 | 0 | nan | nan | nan | nan | nan | nan | 0 | 0 | 0 | nan | nan | nan | nan | nan | nan | 0 | 0 | 0
8 | 4096 | 277 | -3584.9049377441406 | 1.9639501422643661 | 400.0 | -1682.5668084882639 | 4.794169983883126 | 2.2799231222940612 | 0.02053554092489461 | 0.013241797334681102 | 0.02649421696346234 | 0 | 400.0 | -0.001966045703738928 | 8456.784606933594 | -1.7573435604572296 | 0.0002371165028307587 | 7.294169983883126 | 2.2799231222940612 | 2.88 | 0.02053554092489461 | 0.013241797334681102 | 0.02649421696346234 | 0 | 400 | 0 | nan | nan | nan | nan | nan | nan | 0 | 0 | 0 | nan | nan | nan | nan | nan | nan | 0 | 0 | 0 | nan | nan | nan | nan | nan | nan | 0 | 0 | 0
9 | 4608 | 274 | -3584.9049377441406 | 1.9639501422643661 | 400.0 | nan | nan | nan | nan | nan | nan | 0 | nan | -0.0006876524421386421 | 10239.166748046875 | -1.7574053704738617 | 0.00017396104522049427 | nan | nan | nan | nan | nan | nan | 0 | 0 | 0 | nan | nan | nan | nan | nan | nan | 0 | 0 | 0 | nan | nan | nan | nan | nan | nan | 0 | 0 | 0 | nan | nan | nan | nan | nan | nan | 0 | 0 | 0
10 | 5120 | 274 | -3452.342732747396 | 1.9477943579355876 | 400.0 | -1693.0215198054223 | 5.719875859033197 | 2.3207417225627442 | 0.01482233718223186 | 0.012837865007704119 | 0.02544715430326006 | 0 | 400.0 | -0.0007440634071826935 | 5077.909973144531 | -1.7575132548809052 | 7.374471169896424e-05 | 8.219875859033197 | 2.3207417225627442 | 2.88 | 0.01482233718223186 | 0.012837865007704119 | 0.02544715430326006 | 0 | 400 | 0 | nan | nan | nan | nan | nan | nan | 0 | 0 | 0 | nan | nan | nan | nan | nan | nan | 0 | 0 | 0 | nan | nan | nan | nan | nan | nan | 0 | 0 | 0
11 | 5632 | 286 | -3452.342732747396 | 1.9477943579355876 | 400.0 | nan | nan | nan | nan | nan | nan | 0 | nan | -0.0027439576806500554 | 7164.661682128906 | -1.7579286098480225 | 0.00020050897728651762 | nan | nan | nan | nan | nan | nan | 0 | 0 | 0 | nan | nan | nan | nan | nan | nan | 0 | 0 | 0 | nan | nan | nan | nan | nan | nan | 0 | 0 | 0 | nan | nan | nan | nan | nan | nan | 0 | 0 | 0
12 | 6144 | 289 | -3452.342732747396 | 1.9477943579355876 | 400.0 | -1606.9845618222128 | 6.502318414032125 | 2.330221950004881 | 0.01186182456416364 | 0.012382556505583757 | 0.023919973890068117 | 0 | 400.0 | -0.0004942477680742741 | 12020.490234375 | -1.7582336068153381 | 0.0001743751927278936 | 9.002318414032125 | 2.330221950004881 | 2.88 | 0.01186182456416364 | 0.012382556505583757 | 0.023919973890068117 | 0 | 400 | 0 | nan | nan | nan | nan | nan | nan | 0 | 0 | 0 | nan | nan | nan | nan | nan | nan | 0 | 0 | 0 | nan | nan | nan | nan | nan | nan | 0 | 0 | 0
13 | 6656 | 298 | -3433.193862915039 | 1.922471895813942 | 400.0 | nan | nan | nan | nan | nan | nan | 0 | nan | -0.0012337722582742572 | 8240.812072753906 | -1.7586054503917694 | 0.00012096122372895479 | nan | nan | nan | nan | nan | nan | 0 | 0 | 0 | nan | nan | nan | nan | nan | nan | 0 | 0 | 0 | nan | nan | nan | nan | nan | nan | 0 | 0 | 0 | nan | nan | nan | nan | nan | nan | 0 | 0 | 0
14 | 7168 | 298 | -3433.193862915039 | 1.922471895813942 | 400.0 | -1869.801525865114 | 3.454313741705871 | 2.323725160610755 | 0.015648849113474396 | 0.014447770985870533 | 0.030438753082317898 | 0 | 400.0 | -0.0011213363613933325 | 6097.47900390625 | -1.7589855194091797 | 0.00013967108679935336 | 5.954313741705871 | 2.323725160610755 | 2.88 | 0.015648849113474396 | 0.014447770985870533 | 0.030438753082317898 | 0 | 400 | 0 | nan | nan | nan | nan | nan | nan | 0 | 0 | 0 | nan | nan | nan | nan | nan | nan | 0 | 0 | 0 | nan | nan | nan | nan | nan | nan | 0 | 0 | 0
15 | 7680 | 308 | -3433.193862915039 | 1.922471895813942 | 400.0 | nan | nan | nan | nan | nan | nan | 0 | nan | -0.0028393263928592205 | 6811.432373046875 | -1.7588659226894379 | 0.0003381258575245738 | nan | nan | nan | nan | nan | nan | 0 | 0 | 0 | nan | nan | nan | nan | nan | nan | 0 | 0 | 0 | nan | nan | nan | nan | nan | nan | 0 | 0 | 0 | nan | nan | nan | nan | nan | nan | 0 | 0 | 0
16 | 8192 | 301 | -3321.281213378906 | 1.9166076242923737 | 400.0 | -1923.9525527751136 | 1.9340925817916759 | 2.2781177209127845 | 0.017810484606668134 | 0.014874983824078583 | 0.0333863623081582 | 0 | 400.0 | -0.00018089497461915016 | 5378.804382324219 | -1.7586713135242462 | 0.00019282646826468408 | 4.434092581791676 | 2.2781177209127845 | 2.88 | 0.017810484606668134 | 0.014874983824078583 | 0.0333863623081582 | 0 | 400 | 0 | nan | nan | nan | nan | nan | nan | 0 | 0 | 0 | nan | nan | nan | nan | nan | nan | 0 | 0 | 0 | nan | nan | nan | nan | nan | nan | 0 | 0 | 0
17 | 8704 | 309 | -3321.281213378906 | 1.9166076242923737 | 400.0 | nan | nan | nan | nan | nan | nan | 0 | nan | -0.000829917611554265 | 6060.5167236328125 | -1.7586629390716553 | 0.00011316288146190345 | nan | nan | nan | nan | nan | nan | 0 | 0 | 0 | nan | nan | nan | nan | nan | nan | 0 | 0 | 0 | nan | nan | nan | nan | nan | nan | 0 | 0 | 0 | nan | nan | nan | nan | nan | nan | 0 | 0 | 0
18 | 9216 | 308 | -3321.281213378906 | 1.9166076242923737 | 400.0 | -1970.1581092202682 | 2.8195212657797715 | 2.3165693961506224 | 0.014042410233941396 | 0.014205949843292764 | 0.03228142276065742 | 0 | 400.0 | -0.0011372505687177181 | 12776.892456054688 | -1.7585461735725403 | 0.0001479070051573217 | 5.3195212657797715 | 2.3165693961506224 | 2.88 | 0.014042410233941396 | 0.014205949843292764 | 0.03228142276065742 | 0 | 400 | 0 | nan | nan | nan | nan | nan | nan | 0 | 0 | 0 | nan | nan | nan | nan | nan | nan | 0 | 0 | 0 | nan | nan | nan | nan | nan | nan | 0 | 0 | 0
19 | 9728 | 314 | -3355.5431009928384 | 1.9349407603343327 | 400.0 | nan | nan | nan | nan | nan | nan | 0 | nan | -0.001528848777525127 | 11000.01611328125 | -1.7587003707885742 | 0.0001653107174206525 | nan | nan | nan | nan | nan | nan | 0 | 0 | 0 | nan | nan | nan | nan | nan | nan | 0 | 0 | 0 | nan | nan | nan | nan | nan | nan | 0 | 0 | 0 | nan | nan | nan | nan | nan | nan | 0 | 0 | 0
20 | 10240 | 313 | -3355.5431009928384 | 1.9349407603343327 | 400.0 | -1508.841679942888 | 10.315551614900011 | 2.3846195485440074 | 0.005272252326576046 | 0.010667702089760582 | 0.02014086501962349 | 1 | 400.0 | -0.000304914778098464 | 4446.239196777344 | -1.759264975786209 | 0.00010594329796731472 | 10.315551614900011 | 2.3846195485440074 | 2.88 | 0.005272252326576046 | 0.010667702089760582 | 0.02014086501962349 | 1 | 400 | 0 | nan | nan | nan | nan | nan | nan | 0 | 0 | 0 | nan | nan | nan | nan | nan | nan | 0 | 0 | 0 | nan | nan | nan | nan | nan | nan | 0 | 0 | 0
21 | 10752 | 318 | -3355.5431009928384 | 1.9349407603343327 | 400.0 | nan | nan | nan | nan | nan | nan | 0 | nan | -0.0006443849997594953 | 13000.06298828125 | -1.7599467635154724 | 9.737940854392946e-05 | nan | nan | nan | nan | nan | nan | 0 | 0 | 0 | nan | nan | nan | nan | nan | nan | 0 | 0 | 0 | nan | nan | nan | nan | nan | nan | 0 | 0 | 0 | nan | nan | nan | nan | nan | nan | 0 | 0 | 0
22 | 11264 | 316 | -3351.4465767996653 | 1.9250417820044927 | 400.0 | -1994.9899129688893 | 2.9580958894066267 | 2.405234189509379 | 0.01056134942945934 | 0.014588877749662 | 0.033300565607070266 | 0 | 400.0 | -0.0009742106776684523 | 11964.4609375 | -1.7603035867214203 | 7.280934369191527e-05 | 5.458095889406627 | 2.405234189509379 | 2.88 | 0.01056134942945934 | 0.014588877749662 | 0.033300565607070266 | 0 | 400 | 0 | nan | nan | nan | nan | nan | nan | 0 | 0 | 0 | nan | nan | nan | nan | nan | nan | 0 | 0 | 0 | nan | nan | nan | nan | nan | nan | 0 | 0 | 0
23 | 11776 | 323 | -3351.4465767996653 | 1.9250417820044927 | 400.0 | nan | nan | nan | nan | nan | nan | 0 | nan | -0.0030198993626981974 | 5058.650451660156 | -1.7605047523975372 | 0.000306416186504066 | nan | nan | nan | nan | nan | nan | 0 | 0 | 0 | nan | nan | nan | nan | nan | nan | 0 | 0 | 0 | nan | nan | nan | nan | nan | nan | 0 | 0 | 0 | nan | nan | nan | nan | nan | nan | 0 | 0 | 0
24 | 12288 | 322 | -3351.4465767996653 | 1.9250417820044927 | 400.0 | -1667.0487038729057 | 6.192577915065085 | 2.3366394690270504 | 0.011158680855964442 | 0.012512220529419743 | 0.024802475818000474 | 0 | 400.0 | 0.0004987725988030434 | 15493.298583984375 | -1.7606875896453857 | 0.00020274586859159172 | 8.692577915065085 | 2.3366394690270504 | 2.88 | 0.011158680855964442 | 0.012512220529419743 | 0.024802475818000474 | 0 | 400 | 0 | nan | nan | nan | nan | nan | nan | 0 | 0 | 0 | nan | nan | nan | nan | nan | nan | 0 | 0 | 0 | nan | nan | nan | nan | nan | nan | 0 | 0 | 0
25 | 12800 | 327 | -3435.7593002319336 | 1.935438260436058 | 400.0 | nan | nan | nan | nan | nan | nan | 0 | nan | -0.0004034343874081969 | 19807.093994140625 | -1.7608439922332764 | 3.547751111909747e-05 | nan | nan | nan | nan | nan | nan | 0 | 0 | 0 | nan | nan | nan | nan | nan | nan | 0 | 0 | 0 | nan | nan | nan | nan | nan | nan | 0 | 0 | 0 | nan | nan | nan | nan | nan | nan | 0 | 0 | 0
26 | 13312 | 326 | -3435.7593002319336 | 1.935438260436058 | 400.0 | -2024.1141771726586 | 3.0197032056064774 | 2.396553139920862 | 0.012849942325703094 | 0.015143958137239915 | 0.03248105225805794 | 0 | 400.0 | -0.0010454851435497403 | 3475.7960510253906 | -1.7610699236392975 | 8.031466859392822e-05 | 5.519703205606477 | 2.396553139920862 | 2.88 | 0.012849942325703094 | 0.015143958137239915 | 0.03248105225805794 | 0 | 400 | 0 | nan | nan | nan | nan | nan | nan | 0 | 0 | 0 | nan | nan | nan | nan | nan | nan | 0 | 0 | 0 | nan | nan | nan | nan | nan | nan | 0 | 0 | 0
27 | 13824 | 331 | -3435.7593002319336 | 1.935438260436058 | 400.0 | nan | nan | nan | nan | nan | nan | 0 | nan | -0.0012394617078825831 | 5395.586608886719 | -1.761559545993805 | 0.00019336462719365954 | nan | nan | nan | nan | nan | nan | 0 | 0 | 0 | nan | nan | nan | nan | nan | nan | 0 | 0 | 0 | nan | nan | nan | nan | nan | nan | 0 | 0 | 0 | nan | nan | nan | nan | nan | nan | 0 | 0 | 0
28 | 14336 | 331 | -3435.7593002319336 | 1.935438260436058 | 400.0 | -2610.200970122665 | 1.1273475500390115 | 2.42468770184348 | 0.014636085898108919 | 0.018505737901462954 | 0.035538868069557014 | 0 | 400.0 | -0.0004465840756893158 | 7964.5938720703125 | -1.762024313211441 | 0.00010992871830239892 | 3.6273475500390115 | 2.42468770184348 | 2.88 | 0.014636085898108919 | 0.018505737901462954 | 0.035538868069557014 | 0 | 400 | 0 | nan | nan | nan | nan | nan | nan | 0 | 0 | 0 | nan | nan | nan | nan | nan | nan | 0 | 0 | 0 | nan | nan | nan | nan | nan | nan | 0 | 0 | 0
29 | 14848 | 335 | -3359.5135498046875 | 1.9392849604288738 | 400.0 | nan | nan | nan | nan | nan | nan | 0 | nan | -0.0018660637433640659 | 3039.2513122558594 | -1.7624461352825165 | 0.0001911225845105946 | nan | nan | nan | nan | nan | nan | 0 | 0 | 0 | nan | nan | nan | nan | nan | nan | 0 | 0 | 0 | nan | nan | nan | nan | nan | nan | 0 | 0 | 0 | nan | nan | nan | nan | nan | nan | 0 | 0 | 0
30 | 15360 | 335 | -3359.5135498046875 | 1.9392849604288738 | 400.0 | -2672.8567874129767 | 0.8883858544605112 | 2.496310454541767 | 0.017145723275168907 | 0.017532354894316732 | 0.03812098356628181 | 0 | 400.0 | -0.0009499314473941922 | 4448.376708984375 | -1.7630462050437927 | 0.00038774710264988244 | 3.388385854460511 | 2.496310454541767 | 2.88 | 0.017145723275168907 | 0.017532354894316732 | 0.03812098356628181 | 0 | 400 | 0 | nan | nan | nan | nan | nan | nan | 0 | 0 | 0 | nan | nan | nan | nan | nan | nan | 0 | 0 | 0 | nan | nan | nan | nan | nan | nan | 0 | 0 | 0
31 | 15872 | 340 | -3359.5135498046875 | 1.9392849604288738 | 400.0 | nan | nan | nan | nan | nan | nan | 0 | nan | -0.00012377637904137373 | 5812.022888183594 | -1.7632525861263275 | 0.00013798524742014706 | nan | nan | nan | nan | nan | nan | 0 | 0 | 0 | nan | nan | nan | nan | nan | nan | 0 | 0 | 0 | nan | nan | nan | nan | nan | nan | 0 | 0 | 0 | nan | nan | nan | nan | nan | nan | 0 | 0 | 0
32 | 16384 | 337 | -3280.300152587891 | 1.9516239792108536 | 400.0 | -2570.4284049048456 | -0.7992263810690241 | 2.4439947159614275 | 0.015144862543675227 | 0.01832438138302664 | 0.041267016795946826 | 0 | 400.0 | -0.002381164755206555 | 3691.119659423828 | -1.7632390856742859 | 0.00012336013605818152 | 1.700773618930976 | 2.4439947159614275 | 2.88 | 0.015144862543675227 | 0.01832438138302664 | 0.041267016795946826 | 0 | 400 | 0 | nan | nan | nan | nan | nan | nan | 0 | 0 | 0 | nan | nan | nan | nan | nan | nan | 0 | 0 | 0 | nan | nan | nan | nan | nan | nan | 0 | 0 | 0
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

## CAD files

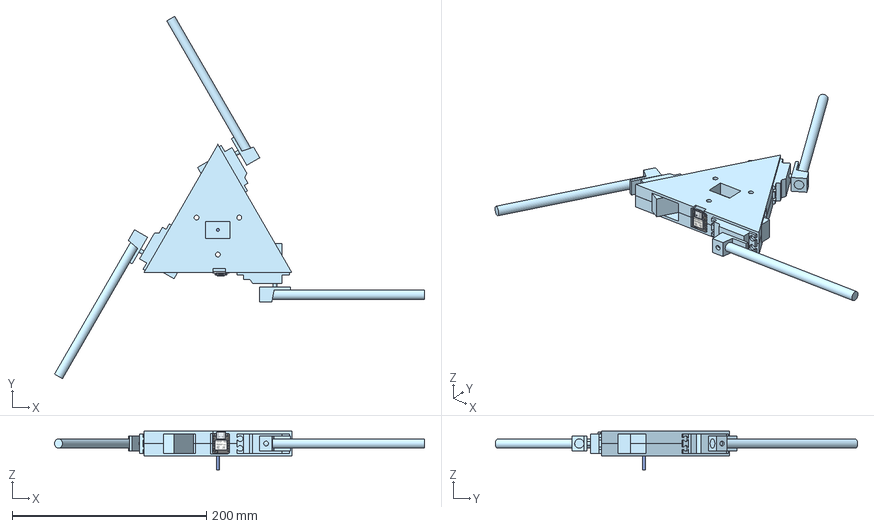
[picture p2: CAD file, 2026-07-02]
CAD/Bram_full_assembly.step
381.2 x 373.4 x 39.7 mm
XIAO-ESP32S3 v2 v2

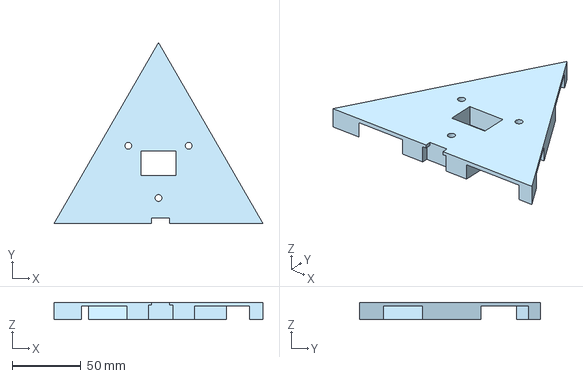
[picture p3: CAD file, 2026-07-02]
CAD/top.step
152.4 x 132.0 x 12.7 mm

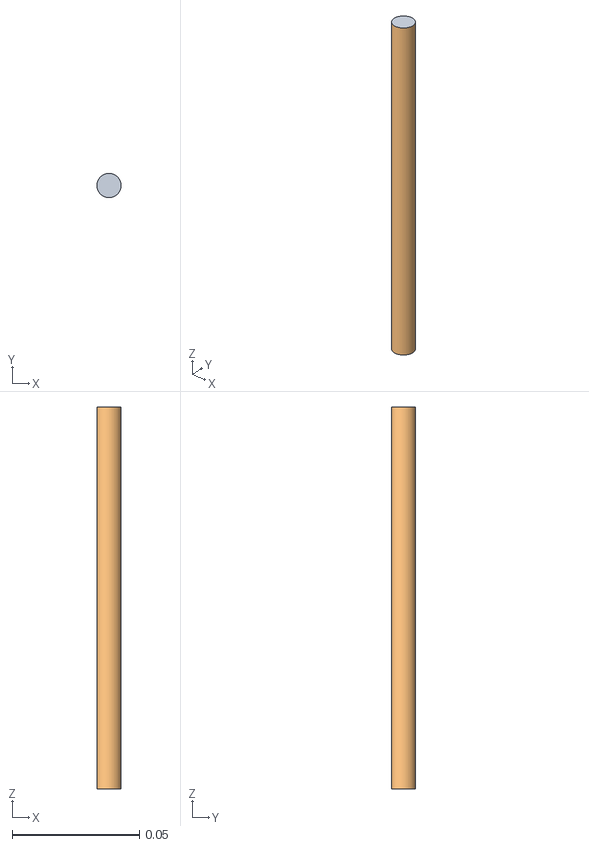
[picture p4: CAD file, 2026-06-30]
software/gait_discovery/assets/15cm_leg.obj
0.00953 x 0.00951 x 0.15

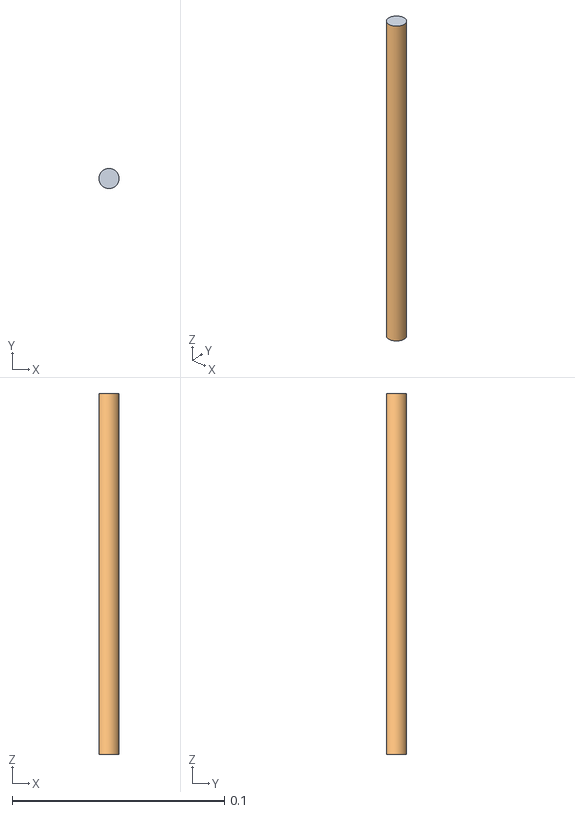
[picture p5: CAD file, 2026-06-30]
software/gait_discovery/assets/17cm_leg.obj
0.00953 x 0.00951 x 0.17

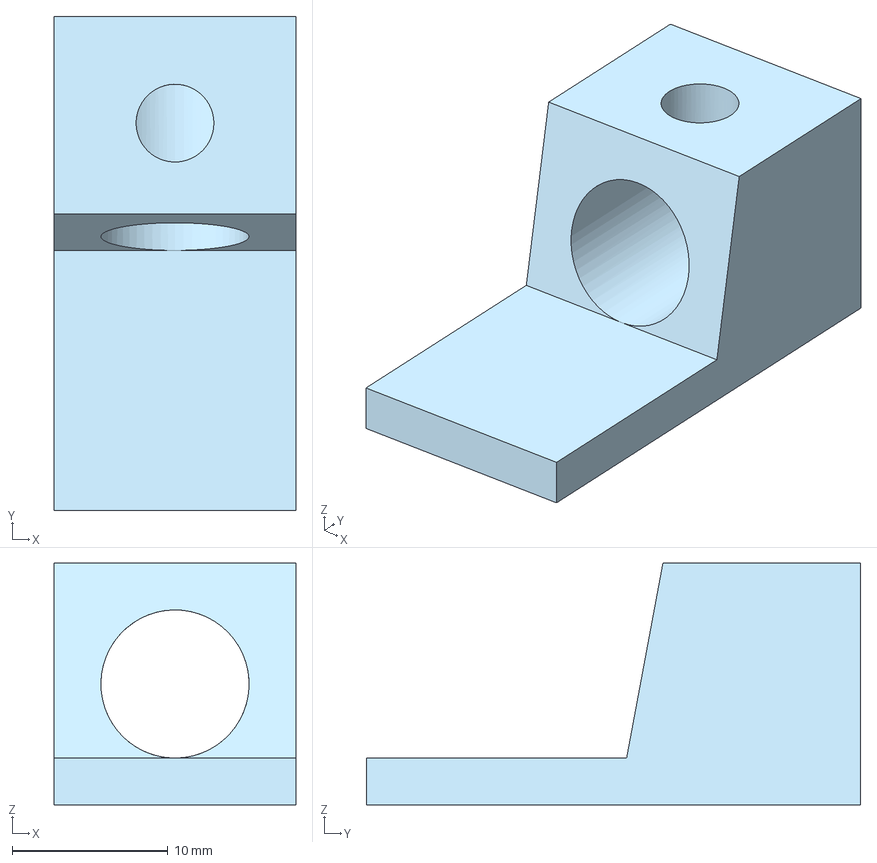
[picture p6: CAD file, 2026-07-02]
CAD/Servo.step
15.5 x 31.8 x 15.5 mm

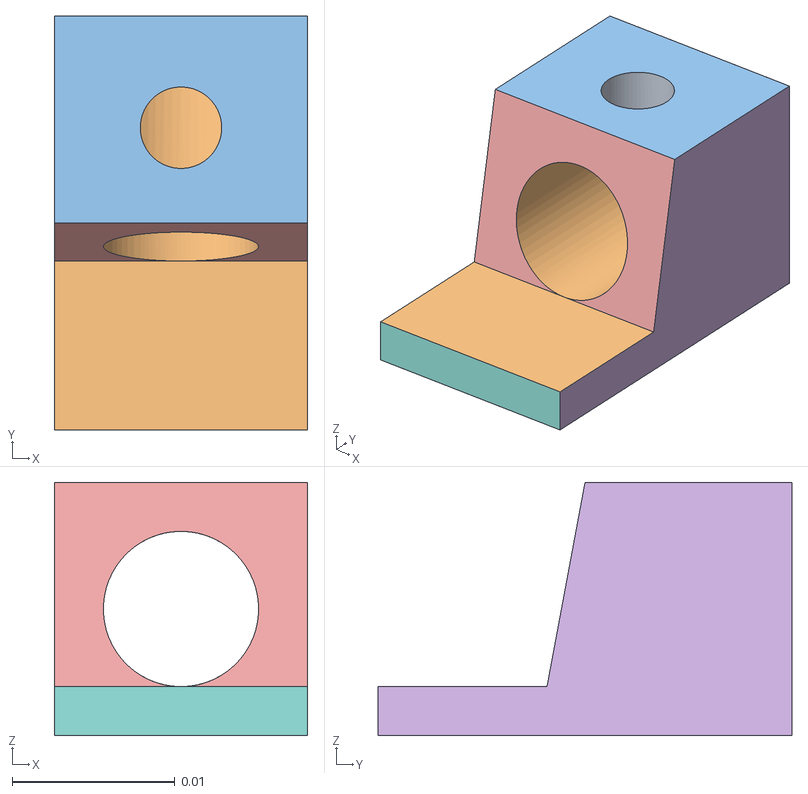
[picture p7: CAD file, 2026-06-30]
software/gait_discovery/assets/servo_adapter.obj
0.0155 x 0.0254 x 0.0155

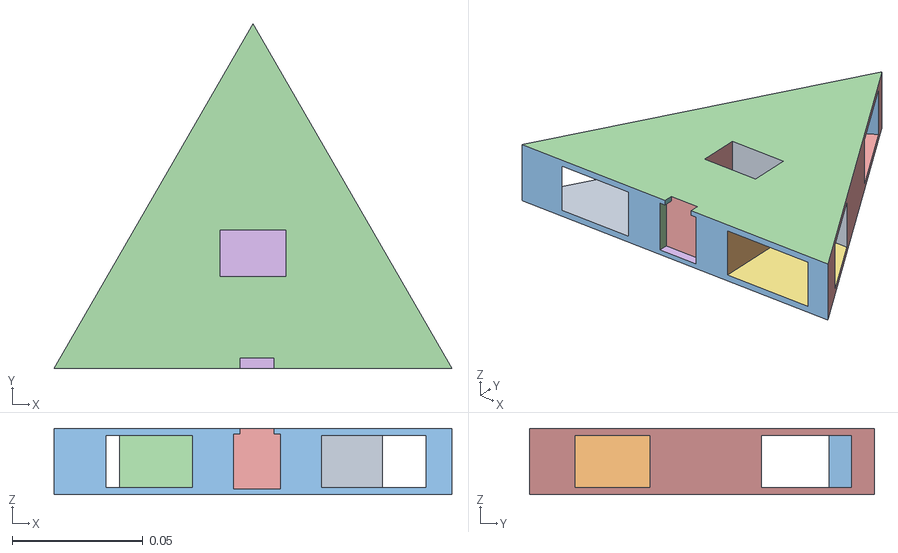
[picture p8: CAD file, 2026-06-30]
software/gait_discovery/assets/chassis.obj
0.152 x 0.132 x 0.0254

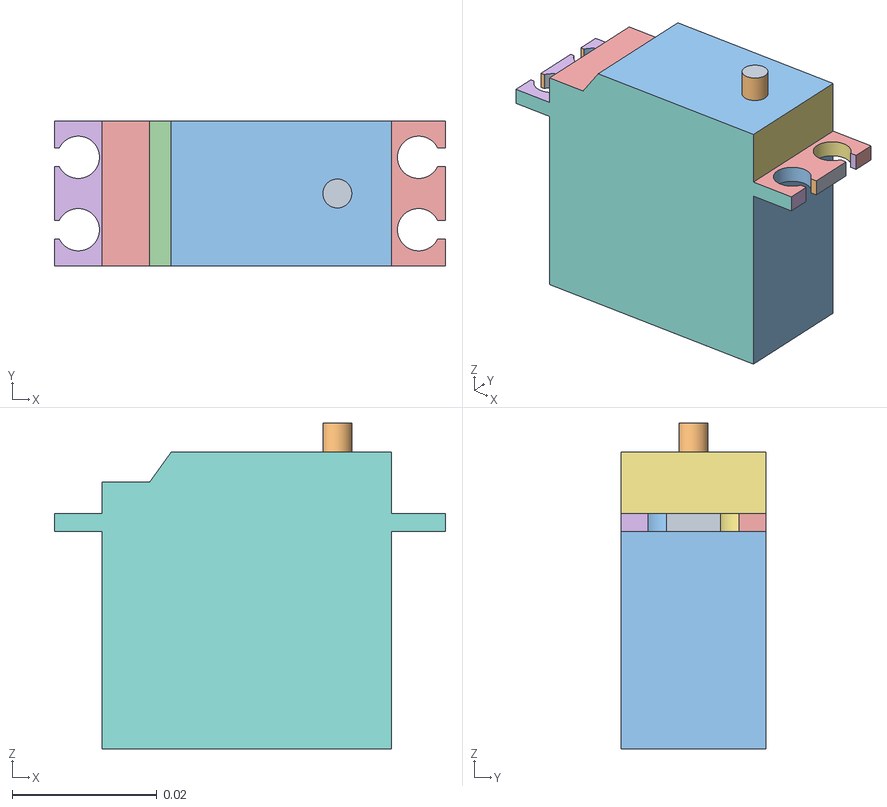
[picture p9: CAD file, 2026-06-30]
software/gait_discovery/assets/servo.obj
0.054 x 0.02 x 0.045

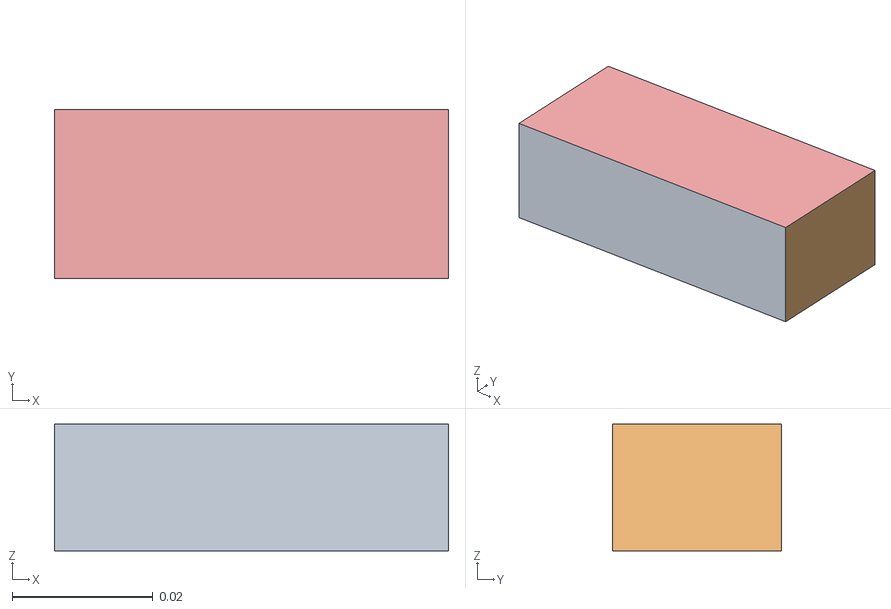
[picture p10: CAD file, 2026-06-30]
software/gait_discovery/assets/battery.obj
0.056 x 0.024 x 0.018

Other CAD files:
CAD/bottom.step

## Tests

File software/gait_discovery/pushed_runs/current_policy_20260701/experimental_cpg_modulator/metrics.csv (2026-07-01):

command | reward | command_distance | line_distance | yaw_distance | x_distance | y_distance | cross_track_error | heading_error | length | terminated
idle | 63.98402581095937 | 0.0 | 0.0 | 0.0 | 5.564188399785655e-05 | 4.9495908495204975e-05 | 4.9495908495204975e-05 | 0.00090217651635216 | 400 | False
fwd1 | 85.44937359930188 | 0.6409412724144843 | 0.6409412724144843 | 0.0 | 0.6409412724144843 | -0.15390990861781564 | -0.15390990861781564 | -0.7050380115984316 | 400 | False
back1 | -271.0692239597958 | -0.3037853557139663 | -0.3037853557139663 | 0.0 | 0.3037853557139663 | 0.249995641525042 | 0.249995641525042 | 0.4545610633553139 | 400 | False
fwd05 | 2.9113867039891703 | 0.13757156499737427 | 0.13757156499737427 | 0.0 | 0.27514312999474855 | -0.05535845954675498 | -0.05535845954675498 | -0.46577344702911816 | 400 | False
back05 | -11.450746704063972 | 0.042070539441259776 | 0.042070539441259776 | 0.0 | -0.08414107888251955 | -0.17532637006080432 | -0.17532637006080432 | -0.2853853021261554 | 400 | False
yaw_l1 | 517.0344204282401 | 0.23146713956751747 | 0.0 | 2.3146713956751737 | 0.15498452455877268 | -0.3096439203750523 | 0.33071310591726366 | -1.0021432971452473 | 400 | False
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

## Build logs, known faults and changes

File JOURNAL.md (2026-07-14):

# JOURNAL.md

## 6/19

Initial mockup!


basically im gonna rl walking or somehting idk ima do some research bu im gonna cad first im gonna use like big servos and mag encoders and my pi 3 and probably a pico also but idk ill see type

in between this was cad and parts, tuff 👍

## 6/29-6/30

Set up the Python/MuJoCo gait-discovery project, built the first usable tripod model from measured geometry, added rough hardware constraints, and trained early PPO policies. Forward locomotion became the first solved behavior, while broad joystick control, yaw, and aggressive sim-to-real noise exposed reward hacking, arcing, stationary local optima, and the need for stricter world-frame command metrics.

## 6/30

Reworked the environment and training process around command obedience, per-command evals, gated curricula, distillation, and straight-line polish. Fixed forward/back/yaw primitives proved individually learnable, but one shared PPO actor was unstable for full joystick control, which pushed the project toward expert distillation, deterministic CPG search, yaw action tables, and hybrid composition rather than a single end-to-end learned policy.

## 7/1

Corrected yaw scoring to use real planar heading instead of body gyro wobble, retrained/exported learned yaw primitives, searched deterministic forward/back CPGs and mixed-arc blend grids, and settled on the current deployable architecture: deterministic forward/back CPGs plus learned left/right yaw tables plus a tuned grid blend for mixed commands. The standalone controller export now lives under the gait_discovery folder and is the source for the future ESP32 port.

7/1 THE EVENING!

Did some minor cad (recessed where the bolts go), added screw holes, to keep the robot together, as my 3d printer is broken and my friend whos printer works leaves on a trip tomorrow, so I had to get my friend to print the parts today.

On architecture: I went through a lot of pivots and eventually landed on a hybrid controller instead of a single end-to-end learned policy. In retrospect, forward and backward crawling made much more sense as deterministic gaits, which I found out empirically after fighting the general PPO setup for a while. The learned PPO-derived yaw behavior was stellar though, so I kept that part and built the final controller around combining deterministic translation with learned turning.

I also dropped the pizero as it was unneccesary the intial policy setup I had planned was already small enough to run on an esp32 like raw, and the one I have right now also is, and it just makes my life easier and I cant even get a pi zero they are like 60 dollars its crazy!
prints!
sim:

prints:



## 7/13 movement_v2 yaw polish

Okay so the old "just train one yaw generalist" thing was kinda cooked for what I actually need on hardware. I only really need base primitives I can bind to the ESP32, and the robot has an IMU, so exporting open-loop tables is not the move. The move is online tiny policies: previous 4 IMU quats + previous 6 servo actions + command/base features in, 3 servo targets/residual out, low-rate policy, servo smoothing outside the policy.

First important thing: the left yaw table export was lying to me. The searched left CPG params were good when held at the original 10 Hz timing, but the interpolated table replay changed the contact timing and drifted like trash. So I changed the residual yaw env so the base can be either a JSON table or the original searched CPG params directly. That mattered a lot.

Left yaw method:

- base: `yaw-left_base_params.json`, direct searched CPG, held at 10 Hz
- residual: small PPO policy around the base, `residual_limit=0.12`, no extra residual slew
- train command: only `yaw_pos1`, not all yaw commands
- run: `software/movement_v2/runs/yaw_left_residual_cpg/yaw_residual_20260713_185146`
- promoted checkpoint: `software/movement_v2/exports/final_yaw_20260713/yaw-left_residual_policy_best.pt`

Left got way cleaner:

- raw direct CPG: `2.297 rad`, `2.70 cm` final drift, `1.11 cm` mean, `3.58 cm` max
- residual best: `2.285 rad`, `0.77 cm` final drift, `1.09 cm` mean, `1.97 cm` max

Then I tried to get right yaw up to that standard. First instinct was "do what worked on left" and try right CPG params directly. I tested the old right search seeds through the same residual wrapper. Seed 41 had strong yaw and good final position (`3.13 rad`, `1.15 cm` final drift), but it wandered mid-rollout (`2.79 cm` mean, `4.99 cm` max), so raw CPG right was not actually the best teacher. Tight-gate residual around that CPG also wasted compute and kept jumping into 5-9 cm peak drift. Basically, do not throw a new CPG search at right yaw just because it worked for left.

The good move was the less glamorous one: take the already-good right residual checkpoint and fine-tune it as a right-only specialist. Starting point was the old promoted right residual:

- old right: `2.341 rad`, `1.63 cm` final drift, `1.40 cm` mean, `2.79 cm` max

Fine-tune method:

- init checkpoint: `yaw-right_residual_policy_best.pt`
- base: `yaw-right_residual_base_table.json`
- train command: only `yaw_neg1`
- `frame_skip=10` / 50 Hz residual env, because this right artifact was table/residual based already
- `residual_limit=0.18`
- `slew_limit=0.25`
- low LR: `5e-5`
- tighter training gate than the old accept gate: `2.0 cm` final, `1.2 cm` mean, `2.2 cm` max
- run: `software/movement_v2/runs/yaw_right_residual_finetune_tight/yaw_residual_20260713_193828`
- promoted checkpoint: `software/movement_v2/exports/final_yaw_20260713/yaw-right_residual_policy_finetuned_best.pt`

That hit the money checkpoint at about 10k steps:

- new right: `2.385 rad`, `0.53 cm` final drift, `1.07 cm` mean, `2.01 cm` max

Compared to left:

- left residual: `2.285 rad`, `0.77 cm` final, `1.09 cm` mean, `1.97 cm` max
- right residual: `2.385 rad`, `0.53 cm` final, `1.07 cm` mean, `2.01 cm` max

So right now beats left on yaw amount, final drift, and mean drift. Left only barely wins max drift by like `0.04 cm`, which is basically tiny but I wrote it down because the metric says it. I also tried a peak-polish run from the new right best with an even tighter max target, but it did not beat the saved checkpoint, so I did not promote it. Good reminder that "stricter" is not automatically better; once the policy is clean, PPO can just trade one metric for another.

The final yaw package is now:

- `software/movement_v2/exports/final_yaw_20260713/manifest.json`
- left full yaw: `yaw-left_residual_policy_best.pt` on direct CPG params
- right full yaw: `yaw-right_residual_policy_finetuned_best.pt` on the right residual base table

Verified with:

```bash
.venv-rl/bin/python software/movement_v2/visualize_final_yaw.py --headless --case suite --seconds 8
```

The actual lesson is kinda important: left wanted CPG-param residual because table export broke timing, but right wanted checkpoint polish because the existing table residual already encoded a good contact pattern. Same residual idea, different best base. This is probably the ontology going forward: primitive-specific base source first, then narrow residual PPO around the best reproducible base, not broad generalist PPO unless there is no other option.

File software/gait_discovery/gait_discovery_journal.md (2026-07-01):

# Gait Discovery Journal

This is the full detailed log of all gait-discovery approaches, including MuJoCo modeling, PPO experiments, reward changes, deterministic gait search, yaw-table export, hybrid controller work, run IDs, and known failures. The root `JOURNAL.md` is now only a brief daily synthesis.

6/19

so the idea is this



basically im gonna rl walking or somehting idk ima do some research bu im gonna cad first im gonna use like big servos and mag encoders and my pi 3 and probably a pico also bu idk ill see type

night 6/29-30

- Set up the Python/MuJoCo project around `bram.xml`.
  Added Python 3 env tooling, MuJoCo viewer entrypoints, PPO training, policy visualization, and PufferLib tests.

- Tried different approaches for the MuJoCo model.
  Codex wrote all the models conversions, after 2 failed attempts at getting it to pull from cad (spatial reasoning isnt there yet) I just fed it the hinge offsets and it worked fine.

- Added realistic-ish hardware constraints.
  Servos were limited to weakened torque around `3.0 Nm`, actuator range was set to about 160 degrees total, and the observation model was kept close to IMU plus servo command history.

- Built a low-sensor Gym environment.
  Observations use gyro, accel, gravity estimate, command, heading error, recent servo actions, and command deltas; reward can use privileged sim state because it is not deployed.

- Started with simple forward reward.
  It learned movement, but body-frame forward reward let the robot arc and still score well.

- Tried heavier sim-to-real noise early.
  Full randomization made learning much worse and exposed reward hacking before the base gait was stable.

- Tried directional/vector command ideas.
  Full direction control was too much too early and confused "move along vector" with "rotate heading"; forward-plus-yaw became the better intermediate target.

- Tried forward/yaw mixed policies.
  Mixed command training exposed catastrophic command failures, especially yaw/rotate cases, so the work narrowed back to forward first.

- Found `command_distance` was not enough for checkpoint selection.
  It was useful as a diagnostic, but it could reward arcing or body-frame progress instead of straight world-frame progress.

- Added heading-aware world-frame reward.
  Forward progress became line progress along the desired heading, with explicit penalties for lateral drift, yaw error, heading error, jitter, airtime, and falling.

- Hit an early-death exploit.
  The policy learned that dying fast could accumulate less negative reward than surviving badly, so terminal penalties and survival-aware eval scoring were added.

- Hit a stochastic lunge failure.
  Some policies moved only with sampled actions while deterministic mean actions collapsed, so deployable deterministic eval became the main sanity check.

- Switched to "gentle parenting" reward shaping.
  The working split was large praise for alive/upright forward progress, firm fall penalties, and ramped-in penalties for heading, drift, jitter, airtime, and tracking.

- Best clean forward policy so far: `runs/ppo_20260630_002841`.
  It reached about `1.93 m` command progress over a full 400-step episode and looked visually pretty straight despite some measured yaw/side drift. 

- Added mild domain-randomization strength.
  Full DR was too harsh, so randomization now scales around nominal values with `--domain-randomization-strength`, defaulting to `0.45`.

- Added late-episode polish costs.
  Smoothness, jerk, hinge velocity, and airtime penalties now ramp later so exploration is not crushed before a gait emerges.

- Best mild domain-randomized policy so far: `runs/ppo_20260630_004158`.
  It reached about `1.19 m` clean eval distance over 400 steps and survived mild randomized tests, but was slower/uglier than the clean demo gait.

- Current conclusion.
  The clean gait is decent; the mild-DR gait is the sim-to-real starting point; the next best step is checkpoint warm-start and fine-tuning the clean policy with mild DR around `0.25-0.35` and lower learning rate. And then after that Yaw policy and then merging them!

Overall productive day, probably could have gone faster had I "multi-agent-orchestrachted" (yuck) but still I got pretty far.
By tomorrow, I want to get the yaw policy working and merging and then I will run a larger run on my old laptop which has a 3050

The architecture has changed since my pitch so I will be running the policy's actor weights onboard the esp32 and that will be it, trying to keep the model pretty small as a result of that (cant find a pi zero 2 w and its more overhead for like marginally better inference / headroom idk pretty stupid on my part) total bom is looking like
servos: 25$ (3x): 75
xiao esp32c3 off amazook: 10
bec: ~7-10$
imu off adafruit: 20
misc hardware (M3 hardware kit): 15

6/30 afternoon

- Made chassis, battery, and servo cans non-contact in MuJoCo.
  Since I do not trust a random PLA/battery friction estimate, the body now acts as visual/mass geometry and the floor interaction is mostly feet/legs instead of fake chassis sledding.

- Changed "alive" into a liberal limit gate.
  The env no longer pays the robot for being upright/alive; it only terminates for battery-side-down-ish orientation, extreme low body height, or invalid sim state.

- Added retroactive training visualization.
  `train_ppo.py` can save snapshots with `--snapshot-interval`, and `visualize_training_run.py` replays those checkpoints in order after the run.

- Found the stationary local optimum.
  With the v4 reward, standing still on forward command scored around `-7`, so PPO learned quiet non-motion instead of risking movement.

- Reworked exploration/reward into `forward_yaw_heading_v5`.
  Added command stall penalties, immediate command-motion bonus, higher movement payoff, lower early regularization, and higher PPO entropy/action std so standing still gets punished harder.

- Current reward direction.
  Command obedience stays primary; next polish should target crawl quality with foot-slip penalties and progress-per-effort rather than generic prettiness.

6/30 evening general-policy rewrite

- Compared the old movers against the newer generalist runs.
  The successful runs were forward specialists with dense progress reward; the failed generalist runs mostly learned lower-penalty stationary behavior.

- Identified forward as the only solved primitive.
  `runs/ppo_20260630_002841` and related v3 runs moved well, while yaw/back/mixed command training still had near-zero command distance.

- Rewrote the env as `forward_yaw_heading_v9`.
  The reward now pays dense forward/yaw progress first, then applies wrong-way, stall, extra-motion, heading, smoothness, and crawl-polish penalties after the robot has a chance to move.

- Slowed the command curriculum.
  Training now stages positive forward, forward/back, yaw-only, gentle arcs, then full joystick commands instead of blending the whole command space too early.

- Updated checkpoint selection.
  Eval defaults to the full 13-command suite, and score now includes command distance so lower-penalty non-motion is less likely to look like the best policy.

- Smoke check result.
  Zero action is now clearly bad for active commands, idle is rewarded for staying still, and a 4k PPO smoke completed with positive early curriculum returns but no learned full general gait yet.

6/30 gated joystick-policy environment work

- Added per-command deterministic eval metrics.
  `metrics.csv` now logs each command separately (`fwd1`, `back1`, yaw signs, half commands, arcs) so average reward cannot hide a broken direction.

- Replaced time-only curriculum with competence gates.
  Randomized-command training now holds stages until deterministic eval passes required command thresholds for consecutive evals.

- Added weak-command oversampling.
  The trainer samples failed command families more often after eval, so backward/yaw failures get more rollout data instead of being hidden by easy forward commands.

- Changed command stages to isolated primitives first.
  The staged order is now forward, backward with forward replay, yaw-left, yaw-right, primitive mix, arcs, then full joystick.

- Rewrote command-sign punishment into `forward_yaw_heading_v10`.
  Wrong signed movement is punished strongly from the start of the episode, because joystick command obedience matters more than crawl smoothness right now.

- Medium-run result.
  Gated 50k runs now expose the bottleneck clearly: forward passes and unlocks stage 1, but backward does not become positive within the remaining 50k budget.

- Backward feasibility check.
  Fixed backward v10 still learns strongly in 50k (`runs/ppo_20260630_185845`, about `1.02 m`), so the issue is curriculum/transfer, not backward being physically impossible.

- Current conclusion.
  The environment is much better instrumented and stricter, but the one-policy curriculum is not solved yet; the next work should focus on longer stage budgets, warm-start/resume support, or stage-specific optimizer handling so backward can be learned without collapsing the forward primitive.

6/30 follow-up on backward transfer

- Tried weak backward contrast during the forward stage.
  A small backward sample rate in stage 0 did not stop the policy from learning a mostly command-agnostic forward gait.

- Tried balanced forward/backward from scratch.
  The policy stayed near stationary over 50k, so the first gate is too hard when both translation signs are equally weighted from random initialization.

- Added `--init-checkpoint` support.
  The trainer can now initialize a run from a compatible checkpoint while using a fresh optimizer, which is useful for staged experiments and later resume/warm-start work.

- Tried warm-starting from a fixed backward expert.
  Starting from `runs/ppo_20260630_185845/policy_best.pt` preserved backward initially but did not learn forward; both signs decayed toward non-motion by 50k.

- Tried command-phase observation features.
  Extra command-times-gait-phase features increased obs dim to 25 but did not improve the 50k translation-sign curriculum and caused less stable eval, so the env was reverted to v10/21-observation.

- Current blocker.
  Fixed forward and fixed backward both learn, but one shared PPO actor does not yet learn reliable signed translation under the mixed command distribution. The next promising direction is probably stage-specific training mechanics (longer stage budgets, lower LR after unlock, or explicit distillation/replay from fixed-command experts), not more reward scalar tweaking.

6/30 distill-then-anchor breakthrough

- Added explicit expert distillation.
  `train_ppo.py` can now collect expert rollouts, behavior-clone one command-conditioned actor, and optionally run BC-only to test representation before PPO.

- Added PPO anti-forgetting controls.
  PPO now supports command-family advantage normalization, expert replay BC, and a frozen post-BC action anchor so updates do not immediately erase learned command modes.

- Verified one compact actor can represent the primitive gaits.
  Primitive-only BC (`runs/ppo_20260630_200631`) fit four experts to very low MSE and passed forward, backward, yaw-left, and yaw-right without PPO.

- PPO from primitive BC finally stayed stable.
  Anchored PPO (`runs/ppo_20260630_200728`) kept all four primitives passing through stage 4, proving the previous collapse was PPO forgetting, not model capacity.

- Added optional arc experts.
  The old v9 arc-forward-left policy still works in v10, so `train_ppo.py` now accepts arc expert checkpoints for distillation and replay.

- Five-expert BC fixed the left-forward arc.
  Adding the arc-forward-left expert (`runs/ppo_20260630_201507`) raised `arc_fl` from failing to about `0.269`; only `arc_bl` remained slightly weak.

- Reached the first full-suite pass.
  Anchored PPO from five-expert BC (`runs/ppo_20260630_201558`) advanced to stage 5 and had a full-pass snapshot at update 40: primitives and all arcs cleared their gates.

- Current best visual checkpoint.
  Use `runs/ppo_20260630_201558/policy_full_pass.pt`; it is copied from the update-40 snapshot because the final scalar-best checkpoint later regressed `arc_bl`.

- Fixed checkpoint scoring.
  Eval score now includes full-command deficit, so future `policy_best.pt` selection should prefer complete command obedience over higher average distance with one failed command.

- Added single-policy command-suite visualization.
  `visualize_policy.py --command-suite` cycles idle, forward/back, yaw, half commands, and arcs for one checkpoint instead of relaunching the viewer per command.

- Headless visualizer verification.
  `runs/ppo_20260630_201558/policy_full_pass.pt` clears the command suite with mean command progress about `0.408`; all 13 commands ran full length with no weak command under the current thresholds.

- Current visual command.
  Run `.venv-rl/bin/python visualize_policy.py --checkpoint runs/ppo_20260630_201558/policy_full_pass.pt --command-suite --episodes 13` to inspect the general joystick policy in the MuJoCo viewer.

6/30 forward/back line polish

- Added a straight-line polish mode.
  `train_ppo.py --straight-line-polish` samples mostly pure forward/back commands and adds lateral velocity, cross-track error, heading drift, and yaw-rate penalties only for those commands.

- Added line-quality eval metrics.
  Per-command metrics now include cross-track and heading error, and checkpoint scoring can include a straight-line score so average command reward does not hide drift.

- First polish run improved the full-suite checkpoint.
  `runs/ppo_20260630_210517` improved straight-line score from about `-80.6` to `-31.6`, with especially better backward tracking.

- Second polish run is the current forward/back candidate.
  `runs/ppo_20260630_210825/policy_best.pt` reached mean command progress about `0.437` across the full command suite and straight-line score about `-26.9`; it is better but not yet rail-straight.

- Current polished visual command.
  Run `.venv-rl/bin/python visualize_policy.py --checkpoint runs/ppo_20260630_210825/policy_straight_polish.pt --command-suite --episodes 13` to inspect the forward/back-polished general policy.

6/30 smooth gait-generator search

- Added black-box gait search.
  `search_gait.py` optimizes a smooth sinusoidal three-servo gait with frequency, per-leg center, amplitude, phase, and second-harmonic terms.

- First forward search found a usable open-loop crawl.
  `runs/gait_search_forward_refine/best_params.json` gets about `0.343 m` in 4 seconds with about `4 mm` terminal cross-track error in the nominal sim.

- Longer forward eval exposes heading drift.
  The same gait gets about `0.622 m` in 8 seconds but drifts to about `0.59 rad` heading error, so hardware should use IMU heading trim rather than pure open-loop.

- Basic robustness check passed.
  With reset/domain randomization enabled, the forward gait averaged about `0.327 m` over 4 seconds across three episodes without terminating.

- Added heading-corrected gait parameters.
  `search_gait.py` now supports heading/yaw-rate feedback terms that trim the smooth gait using the same heading error and gyro yaw rate a 9DoF IMU would provide.

- First heading-corrected forward gait improved the 8-second line.
  `runs/gait_search_forward_heading/best_params.json` gets about `0.800 m` in 8 seconds with about `5.9 cm` cross-track error and `0.10 rad` final heading error.

- Current correction note.
  The short search mostly selected yaw-rate damping instead of absolute heading Kp; on hardware, heading Kp should remain available and be tuned against the real steering direction.

- Added inverse-seeded backward search.
  `search_gait.py --init-inverse` can seed backward from a forward gait by phase-inverting the smooth waveform, then refine it independently.

- Current backward gait.
  `runs/gait_search_backward_heading_refine/best_params.json` gets about `1.686 m` backward in 8 seconds with about `4.8 cm` cross-track error and `0.31 rad` heading error; randomized 4-second eval averaged about `0.565 m`.

- Current yaw-left gait.
  `runs/gait_search_yaw_left/best_params.json` rotates about `4.28 rad` in 4 seconds with about `8.6 cm` planar drift; randomized eval averaged about `4.54 rad`.

- Current yaw-right gait.
  `runs/gait_search_yaw_right/best_params.json` rotates about `3.68 rad` in 4 seconds with about `11.9 cm` planar drift; randomized eval averaged about `3.63 rad`.

- Tried cloning PPO yaw into the smooth sine gait.
  `fit_policy_gait.py` records PPO actions and fits the smooth gait formula, but the fit collapses toward the mean action because PPO yaw is high-variance/feedback-like rather than a clean time-only waveform.

- Added direct PPO action-table export.
  `export_policy_table.py` records deterministic PPO actions into a 50 Hz table that can be replayed or ported to firmware as a lookup/interpolation gait.

- Current PPO yaw table result.
  From `runs/ppo_20260630_210825/policy_straight_polish.pt`, yaw-right table replay gets about `5.14 rad` in 4 seconds with about `3.7 cm` planar drift; yaw-left gets about `1.20 rad` but drifts about `36 cm`, so yaw-left still needs a better source policy or a separate mirror/refinement.

- Tried mirroring yaw-right into yaw-left.
  `mirror_policy_table.py` brute-forces servo sign flips, rear swaps, time reversal, phase shifts, and optional full servo permutations from the good yaw-right table.

- Best mirrored yaw-left result.
  `runs/policy_table_yaw_left_mirror/yaw-left_mirrored_table.json` gets about `0.98 rad` in 4 seconds with about `13 cm` planar drift; this is cleaner than the bad yaw-left PPO table but far weaker than yaw-right.

6/30 hybrid CPG + learned residual BC

- Added BC hybrid controller.
  `train_hybrid_bc.py` keeps deterministic CPG forward/back as the base action and trains a small residual network that is hard-gated by yaw command, so pure forward/back and idle cannot be modified by the learned layer.

- First obs-based residual was too weak.
  `runs/hybrid_bc_merged_v1` fit the dataset but yaw collapsed in rollout, likely because small action errors changed the env observations the residual depended on.

- Switched to phase/command residual features.
  The better version uses command, base action, previous action, and phase harmonics instead of full IMU/env obs, making the learned yaw residual behave like a compact learned waveform.

- Current BC baseline.
  `runs/hybrid_bc_phase_v2/hybrid_bc_current.pt` completes the command suite with no terminations: forward `0.408 m`, backward `0.795 m`, yaw-left `5.15 rad`, yaw-right `2.43 rad` over 4 seconds.

- Balanced variant was not selected.
  `runs/hybrid_bc_phase_v4` made pure yaw-left/right more balanced (`3.31/2.58 rad`) but terminated on `arc_bl`, so it is less safe as the current checkpoint.

- Remaining BC issues.
  Half-speed forward/back are still weak because amplitude-scaled CPGs do not crawl well at low magnitude, and yaw-right still under-reproduces the raw PPO yaw-right table (`5.14 rad`).

- RL fine-tune decision.
  Do not start residual RL yet; first fix low-speed CPG scaling or discover dedicated half-speed gaits, then add better arc teachers so RL is not asked to repair bad supervised targets.

- Fixed hybrid viewer freeze.
  `train_hybrid_bc.py --view` now resets the same MuJoCo env instead of recreating it under an active viewer, and `--view-command` can jump directly to a specific command like `yaw_l1` or `fwd1`.

- Added pure-yaw direct bypass.
  Pure yaw commands now bypass the residual network and use the best direct yaw sources: searched yaw-left and PPO-table yaw-right.

- Current pure-yaw result after bypass.
  With `runs/hybrid_bc_phase_v2/hybrid_bc_current.pt`, yaw-left is about `4.28 rad` in 4 seconds with about `8.6 cm` planar drift, and yaw-right is about `5.14 rad` with about `3.7 cm` planar drift.

6/30 15 cm symmetric model retest

- Fixed the remaining leg-length asymmetry.
  `bram.xml` now uses the same 15 cm tube/tip geometry for all three legs; the old back-right leg was longer than the others.

- Fresh PPO yaw-left still failed from scratch.
  `runs/ppo_yaw_left_15cm/ppo_20260630_233657` reached only about `0.88 rad` yaw in direct rollout with about `30 cm` planar drift, so the geometry bug was not the full left-yaw problem.

- Fresh PPO yaw-right learned strongly.
  `runs/ppo_yaw_right_15cm/ppo_20260630_233657` reached about `12.12 rad` yaw in direct rollout with about `27 cm` planar drift; high yaw rate, but still too much absolute drift for a clean firmware primitive.

- Old yaw artifacts changed under the corrected model.
  The searched yaw-left gait improved to about `4.19 rad` with about `5.4 cm` drift, while the old yaw-right action table degraded to about `2.14 rad` with about `9 cm` drift.

- Current conclusion.
  The asymmetric leg was a real model bug, but left/right yaw learning is still not equivalent; do not keep training yaw-left PPO from scratch without seeding it from the searched gait or using a residual/teacher setup.

7/1 body-height limit

- Added an aggressive no-body-drag constraint.
  The MuJoCo env now terminates when chassis center height drops below `3.5 cm` and starts penalizing below `5.0 cm`.

- Wired height into gait scoring.
  `search_gait.py` and `mirror_policy_table.py` now track min height plus warning/hard height deficits, so search and table audits reject low chassis gaits.

- Invalidated the latest strict left-yaw candidate.
  `runs/gait_search_yaw_left_strict_15cm/best_params.json` now terminates after `22` steps with `min_height=0.03475 m`, so it was relying on dropping too low.

7/1 height-limited yaw retraining

- Added target-rate yaw scoring.
  Yaw search now scores against the commanded yaw distance instead of rewarding unbounded spin, so overspin cannot hide drift.

- Kept right yaw PPO.
  The right yaw PPO remains the trusted right primitive; the partial right search was stopped rather than replacing a visually good policy.

- Dedicated left-yaw PPO still failed.
  `runs/ppo_yaw_left_height_v1/ppo_20260701_085732` was warm-started from the good right-yaw PPO, but ended at only about `0.020` command distance after 50k steps.

- Left yaw v1/v2 search found feasibility.
  `runs/gait_search_yaw_left_height_v1` found safe but weak yaw (`2.19 rad`), then `height_v2` found target-speed yaw but with too much drift (`5.15 rad`, `13.8 cm` planar drift).

- Current left yaw primitive.
  `runs/gait_search_yaw_left_height_v3_lowdrift/best_params.json` gets about `4.94 rad` against a `4.8 rad` target over 4 seconds, with about `3.0 cm` final planar drift, `5.9 cm` max drift, `min_height=3.66 cm`, and no hard height violation.

- Updated hybrid defaults.
  `train_hybrid_bc.py` now defaults yaw-left to the height-limited low-drift gait and yaw-right to the 15 cm PPO-exported table.

- Longer left-yaw follow-up.
  `height_v4_8s` and `height_v5_lowpathdrift` searched longer 8-second holds; v5 survives 8 seconds with about `8.96 rad` yaw, `5.3 cm` final drift, and `6.5 cm` max drift, but its 4-second endpoint drift is about `11.3 cm`.

- Mixed-horizon search was not selected.
  `height_v6_mixed` evaluated both 4-second and 8-second horizons, but ended with worse endpoint drift (`8.8 cm` at 4 seconds and `10.5 cm` at 8 seconds), so it is not the current default.

- Current left-yaw recommendation.
  Use `height_v3_lowdrift` for short viewer/command-suite tests and compare `height_v5_lowpathdrift` only if testing sustained 8-second yaw holds.

7/1 left PPO level-penalty test

- Added explicit levelness reward pressure.
  `bram_env.py` now penalizes chassis tilt angle directly via `level_penalty`, with a stronger cost after about `0.18 rad` of roll/pitch tilt.

- Fresh left-yaw PPO still failed.
  `runs/ppo_yaw_left_level_v1/ppo_20260701_113309` trained for 50k steps from scratch under the level penalty, but best headless eval only reached about `0.047` command progress over a full 400-step episode.

- Conclusion.
  Levelness penalty reduces the incentive to twitch/tilt, but by itself it makes PPO settle into weak near-stationary motion instead of discovering left yaw; left yaw likely needs an action prior/residual/teacher from a deterministic gait rather than plain PPO from scratch.

7/1 planar-yaw metric fix

- Found the yaw-score bug.
  The env was integrating MuJoCo gyro `z` as yaw progress; chassis rocking/tilting can create body-frame gyro-z without meaningful planar heading change.

- Changed yaw progress to projected heading delta.
  `bram_env.py` now computes `planar_yaw_rate` from wrapped chassis heading change between steps and uses that for `yaw_progress`, `yaw_error`, `yaw_distance`, and command distance; gyro-z is kept only as `gyro_yaw_rate` diagnostics.

- Invalidated previous left-yaw gait scores.
  `runs/gait_search_yaw_left_height_v3_lowdrift/best_params.json` drops from the old apparent `4.94 rad` to only about `0.33 rad` of real planar yaw over 4 seconds, confirming the visual wobble complaint.

- Right yaw remains real.
  `runs/policy_table_yaw_right_15cm/yaw-right_policy_table.json` still replays about `7.07 rad` of planar yaw over 4 seconds under the fixed metric, though it drifts about `15 cm`.

- Removed invalid left-yaw default.
  `train_hybrid_bc.py` no longer defaults to the old left-yaw gait; left yaw needs retraining under the planar-yaw metric before being used as a direct primitive.

7/1 planar-yaw left retraining

- Broad deterministic search failed under real planar yaw.
  `runs/gait_search_yaw_left_planar_v1` mostly terminated early and found only about `0.011 rad` of real left yaw, confirming the old sine gait was not a valid seed.

- Mirroring right yaw was not enough.
  `runs/policy_table_yaw_left_mirror_planar_v2_allperm` tried all servo permutations/signs/time shifts from the real right-yaw table; the best result was only about `1.17 rad` left yaw against a `4.8 rad` target.

- Boosted PPO yaw reward after fixing the metric.
  `bram_env.py` now uses `forward_yaw_heading_v14_planar_yaw_boost`, with stronger reward for real planar yaw, stronger wrong-way yaw penalty, and more translation penalty during rotate-in-place.

- PPO finally learned real left yaw.
  `runs/ppo_yaw_left_planar_v1/ppo_20260701_114808/policy_best.pt` reaches about `0.428` command progress, meaning about `4.28 rad` real planar left yaw over 8 seconds.

- Short fine-tune barely improved it.
  `runs/ppo_yaw_left_planar_v2_finetune/ppo_20260701_115304/policy_best.pt` reaches about `0.433` command progress, or about `4.33 rad` over 8 seconds, but still drifts about `17 cm`; this is real yaw but not yet a clean primitive.

7/1 CPG-modulator policy attempt

- Added a CPG-modulator training/view script.
  `train_cpg_modulator.py` trains a single command-conditioned controller where forward/back are deterministic CPG carriers and yaw is learned as gated CPG parameter/action modulation.

- Exported the 300k left-yaw PPO teacher.
  `runs/policy_table_yaw_left_planar_300k_8s/yaw-left_policy_table.json` replays about `4.62 rad` of real left yaw over 8 seconds.

- Found the previous backward default was stale.
  `runs/gait_search_backward_heading_refine` now moves the wrong way under the current model; `runs/gait_search_backward_rough` still moves backward about `0.90 m` over 8 seconds and is now the modulator script default.

- CPG-param NN compression is not good enough yet.
  Runs `cpg_param_v1` through `v4` reduce action clone error, but the learned approximation loses too much yaw authority; v4 only reaches about `2.31 rad` left yaw versus the exact teacher's `4.62 rad`.

- Exact component-controller review mode works for primitives, not arcs.
  `train_cpg_modulator.py --teacher-controller` runs exact forward/back CPG plus exact yaw tables; idle, forward, full backward, and pure yaw are reviewable, but naive mixed forward+yaw blending still terminates or underperforms.

7/1 residual PPO over component controller

- Added residual PPO trainer.
  `train_residual_ppo.py` freezes the exact component controller as the base action and trains a small PPO policy that outputs only a gated residual; the residual gate is zero for pure forward/back/yaw so solved primitives stay unchanged.

- Made checkpoint scoring arc-focused.
  Eval now reports `arc_score`, `arc_cmd`, and weighted `score`; this avoids hiding bad mixed-command behavior behind good primitive scores.

- Smoke and checkpoint reload pass.
  `runs/residual_ppo_smoke/residual_ppo_20260701_140757/residual_policy_best.pt` reloads and evaluates correctly, proving the training/save/view path works.

- Short 4k pilot shows the right direction but is not solved.
  `runs/residual_ppo_pilot/residual_ppo_20260701_140851/residual_policy_best.pt` improved arc score from about `-0.068` to `-0.026` at the best checkpoint while preserving primitives, but arcs are still not visually final.

- Next larger run command.
  `.venv-rl/bin/python -u train_residual_ppo.py --total-steps 50000 --num-envs 4 --rollout-steps 256 --eval-interval 10 --eval-episodes 1 --output-dir runs/residual_ppo_arc --torch-threads 2 --snapshot-interval 10`

7/1 residual PPO carrier fix

- Naive mixed base was the main arc crash.
  The original residual PPO used the naive component blend for arcs, so `arc_fl` hit the body-height termination at step 24; diagnostics showed `below_body_limit=True` with height around `0.034 m`.

- Switched mixed commands to a safe CPG carrier.
  `train_residual_ppo.py` now uses pure forward/back CPG as the base for mixed forward+yaw commands and leaves pure yaw on the exact yaw tables; zero-residual mixed commands now survive all four arc evals for 400 steps.

- Added focused arc sampling and arc-score checkpointing.
  Training now oversamples the exact four eval arcs, weights `arc_fl` highest, and selects best checkpoints by `arc_score` instead of primitive-dominated aggregate score.

- Best current residual checkpoint.
  `runs/residual_ppo_arc_command/residual_ppo_20260701_141701/residual_policy_best.pt` reaches `arc_score=0.0108`, `arc_cmd=0.0343`, and all arcs survive 400 steps; this is a real improvement over crashy arcs but still weak joystick obedience.

- Longer resume did not help.
  `runs/residual_ppo_arc_command_resume/residual_ppo_20260701_141847` degraded and reintroduced some arc termination, so do not promote it over the shorter command-focused best checkpoint.

7/1 residual scaled-arc controller

- Scalar yaw-table residuals are the best mixed-command baseline so far.
  A safe forward/back CPG carrier plus command-specific scaled yaw-table residuals keeps all four arc commands alive for 400 steps and reaches `arc_score=0.1598`, with scales `fl=-0.20`, `fr=-0.50`, `bl=-0.40`, `br=-0.40`.

- Yaw action must be an explicit policy feature.
  BC without the yaw-table action could not clone the scaled residual timing; adding `yaw_action` to the residual policy observation made supervised cloning work.

- Best learned residual checkpoint is the yaw-feature BC model.
  `runs/residual_bc_scaled_arc_yawfeat/residual_ppo_20260701_142533/residual_policy_best.pt` reaches `arc_score=0.1391`, `arc_cmd=0.1619`, and preserves the solved primitive commands.

- PPO fine-tuning did not improve the BC model.
  `runs/residual_ppo_arc_yawfeat_finetune/residual_ppo_20260701_142606/residual_policy_best.pt` tops out at `arc_score=0.1324`, so keep the BC checkpoint as the current learned best and the scaled controller as the current teacher.

7/1 improved arc teacher and DAgger distillation

- Added arc-controller JSON support.
  `train_residual_ppo.py` can now load `--arc-controller` files with per-quadrant `base_scale`, three servo-specific `yaw_scales`, and `step_offset`; primitives still use the exact forward/back CPG and yaw tables.

- Added `search_arc_controller.py`.
  The search optimizes the small mixed-command teacher directly instead of asking PPO to rediscover arcs; it keeps the controller ESP32-friendly because the policy surface is still tiny.

- Improved the deterministic mixed-command teacher.
  `runs/arc_controller_search/arc_controller_20260701_143909/best_arc_controller.json` reaches `arc_score=0.2906`, `arc_cmd=0.2996`, up from the scalar teacher's `arc_score=0.1598`.

- Plain BC was not enough for the richer teacher.
  A 96-hidden clone reached only `arc_score=0.0765`, and a longer 160-hidden clone reached `arc_score=0.1341`; low supervised loss did not prevent closed-loop rollout drift.

- Added explicit command features and DAgger-style residual distillation.
  The residual policy input now includes the command, and pretraining can collect learner-visited states labeled by the deterministic teacher via `--residual-dagger-rounds`.

- Best current learned residual policy.
  `runs/residual_dagger_arc_controller_weighted/residual_ppo_20260701_144648/residual_policy_best.pt` reaches `arc_score=0.2736`, `arc_cmd=0.2834`, close to the improved teacher while preserving the solved primitive commands.

7/1 broad joystick-grid eval and training

- Added broad mixed-command eval coverage.
  `train_residual_ppo.py --eval-suite broad` now evaluates a 4x4 magnitude grid over all forward/yaw sign quadrants, and `--view-command broad` can cycle the same commands visually.

- The corner-focused policy does not generalize enough.
  The previous best learned residual scores `arc_score=0.2736` on the core four arcs but only `arc_score=0.0638` on the broad joystick grid.

- Added broad quadrant search.
  `search_arc_controller.py --command broad_all` optimizes each quadrant's tiny arc-controller parameters over all mixed magnitudes instead of only the `0.7/0.7` corner.

- Best current broad deterministic teacher.
  `runs/arc_controller_search/arc_controller_20260701_145334/best_arc_controller.json` improves broad teacher score from `arc_score=0.1040` to `arc_score=0.1503`, but its core four-arc score is lower than the corner-focused teacher.

- Best current broad learned policy.
  `runs/residual_dagger_broad_arc_controller/residual_ppo_20260701_151038/residual_policy_best.pt` reaches broad `arc_score=0.1279`, up from the previous learned broad `0.0638`; its core four-arc score is `0.1901`, so keep the earlier `144648` checkpoint for sharp corner-arc demos.

- Dataset cap cleanup.
  `--residual-dataset-max-samples` now caps the initial BC dataset as well as DAgger-augmented datasets, which keeps broad-grid clone runs from silently collecting oversized supervised buffers.

7/1 magnitude-aware grid controller

- Added magnitude-aware arc-controller grid support.
  Arc-controller JSON entries can now include per-quadrant `grid` params keyed like `f0p70_y0p90`; `train_residual_ppo.py` interpolates grid params for arbitrary joystick magnitudes.

- Added grid-point search mode.
  `search_arc_controller.py --command grid_all` optimizes individual mixed-command grid points while preserving the older quadrant-level defaults for interpolation fallback.

- Best current deterministic joystick teacher.
  `runs/arc_controller_grid/arc_controller_20260701_151532/best_arc_controller.json` reaches broad `arc_score=0.2110`, up from the broad quadrant teacher's `0.1503`; it also reaches core `arc_score=0.3634`, beating the earlier corner-focused deterministic teacher.

- Learned grid clone improved but lost too much authority.
  `runs/residual_dagger_grid_arc_controller/residual_ppo_20260701_152801/residual_policy_best.pt` reaches broad `arc_score=0.1512`, better than the previous broad learned `0.1279`, but core `arc_score=0.1704`; for visual review and near-term control, prefer the deterministic grid controller.

- Current interpretation.
  The best ESP32-friendly path is now command -> magnitude-grid interpolation -> CPG/yaw-table function -> servo output; a learned residual clone is optional polish, not the best controller yet.

7/1 standalone controller export

- Added standalone deterministic runtime.
  `bram_controller.py` computes normalized servo commands from `(forward, yaw, step, heading_error, yaw_rate)` using only JSON data and NumPy; it does not require MuJoCo.

- Verified runtime parity.
  Sampled mixed, pure yaw, pure forward, and idle commands match the `train_residual_ppo.py` deterministic grid-controller path with `max_diff=0.0`.

- Added combined export artifact.
  `exports/bram_grid_controller_export.json` bundles forward/back gait params, yaw tables, grid arc-controller params, dt, scaling, and command metadata into one file for later ESP32/C++ translation.

- Current deployable control shape.
  Runtime loop is `read command + IMU -> BramGridController.action(...) -> map [-1, 1] to servo pulse/range`; heading correction is only active for pure forward/back at the moment.

7/1 right-yaw retraining

- Retrained right yaw under the planar-yaw PPO reward.
  `runs/ppo_yaw_right_planar_300k/ppo_20260701_154021/policy_best.pt` was trained with the same 300k-step settings as the good left-yaw run, but the raw exported table overspun at about `15.15 rad` over 8 seconds.

- Chose a scaled right-yaw table for review.
  `runs/policy_table_yaw_right_planar_300k_8s_scaled_0p4/yaw-right_policy_table.json` gives about `7.04 rad` over 8 seconds with about `3.4 cm` planar drift, much cleaner than the old right table.

- Retuned right-side mixed arcs for the new table.
  `runs/arc_controller_grid_right_yaw_0p40/arc_controller_20260701_155840/best_arc_controller.json` updates the `arc_fr` and `arc_br` grid points; core right arcs improved, but broad joystick score is still below the older all-grid controller.

- Updated defaults.
  `bram_controller.py`, `train_cpg_modulator.py`, and `train_hybrid_bc.py` now point right yaw at the scaled planar table; `bram_controller.py` also points at the right-yaw-retuned arc grid.

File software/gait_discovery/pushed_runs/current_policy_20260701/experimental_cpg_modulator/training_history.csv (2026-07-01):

epoch | train_loss | mean_abs_action_error
1.0 | 0.13807228633335658 | 0.17786003606660025
20.0 | 0.04752645609634263 | 0.11080464848450251
40.0 | 0.03181041425892285 | 0.08974215622459139
60.0 | 0.021245992609432766 | 0.07328144077743803
80.0 | 0.015598233656159468 | 0.06234454640320369
100.0 | 0.011972339318266937 | 0.05445930021149772
120.0 | 0.00998644634549107 | 0.04982955210975238
140.0 | 0.008173680544963905 | 0.04515155319656645
160.0 | 0.007804950659296342 | 0.044198832554476604
180.0 | 0.006154210280094828 | 0.03947942544307027
200.0 | 0.005551740779940571 | 0.03760587189878736
220.0 | 0.005037941650620529 | 0.03606952482036182
240.0 | 0.004194427328184247 | 0.03303372732230595
260.0 | 0.0038128777473632777 | 0.031468969051327025

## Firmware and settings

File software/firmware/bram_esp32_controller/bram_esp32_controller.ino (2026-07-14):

#include <Arduino.h>

#ifndef BRAM_ENABLE_BLUEPAD32
#define BRAM_ENABLE_BLUEPAD32 0
#endif

#ifndef BRAM_ENABLE_BLE_COMMANDS
#define BRAM_ENABLE_BLE_COMMANDS 1
#endif

#ifndef BRAM_ENABLE_BNO08X_POLICY_IMU
#define BRAM_ENABLE_BNO08X_POLICY_IMU 0
#endif

#if BRAM_ENABLE_BLUEPAD32
#include <Bluepad32.h>
#endif

#if BRAM_ENABLE_BNO08X_POLICY_IMU
#include <Wire.h>
#include <Adafruit_BNO08x.h>
#endif

#if BRAM_ENABLE_BLE_COMMANDS
#include <BLE2902.h>
#include <BLEDevice.h>
#include <BLEServer.h>
#include <BLEUtils.h>
#endif

#include "bram_controller.hpp"
#include "bram_policy_controller.hpp"

float clipFloat(float value, float low, float high);

// Demo input switch. Leave native BLE commands as the default Arduino path;
// flip this to true for USB serial bring-up commands like: f 0.5 y -0.3.
static constexpr bool kUseSerialInput = false;
static constexpr bool kAllowSerialOverride = true;

static constexpr bool kPrintDebug = true;
static constexpr bool kUseImuCorrection = false;
static constexpr bool kUseOnlinePolicies = true;
static constexpr bool kUseBaseControllerForYaw = true;

static const char* kBleDeviceName = "BRAM";
static const char* kBleServiceUuid = "6e400001-b5a3-f393-e0a9-e50e24dcca9e";
static const char* kBleRxUuid = "6e400002-b5a3-f393-e0a9-e50e24dcca9e";
static const char* kBleTxUuid = "6e400003-b5a3-f393-e0a9-e50e24dcca9e";

static constexpr float kGamepadAxisScale = 512.0f;
static constexpr bool kInvertGamepadForward = true;
static constexpr bool kInvertGamepadYaw = false;

// when i wire
static constexpr int kFrontServoPin = 4;
static constexpr int kBackLeftServoPin = 5;
static constexpr int kBackRightServoPin = 18;

static constexpr int kServoPins[3] = {
    kFrontServoPin,
    kBackLeftServoPin,
    kBackRightServoPin,
};

// Tune these after checking the linkage. Start conservative if anything binds.
static constexpr int kServoMinUs[3] = {1000, 1000, 1000};
static constexpr int kServoNeutralUs[3] = {1500, 1500, 1500};
static constexpr int kServoMaxUs[3] = {2000, 2000, 2000};
static constexpr bool kServoInvert[3] = {false, false, false};

static constexpr int kPwmHz = 50;
static constexpr int kPwmResolutionBits = 16;
static constexpr int kPwmChannels[3] = {0, 1, 2};
static constexpr uint32_t kControlPeriodMs = 25;
static constexpr uint32_t kInputTimeoutMs = 600;
static constexpr float kDeadband = 0.08f;
static constexpr float kCommandSlewPerTick = 0.08f;
static constexpr bool kBlendMixedCommands = false;
static constexpr bool kPrioritizeTranslationWhenMixed = true;
static constexpr uint32_t kPolicyHoldTicks = 2;

bram::BramController controller;
bram::BramPolicyController policyController;

float targetForward = 0.0f;
float targetYaw = 0.0f;
float commandForward = 0.0f;
float commandYaw = 0.0f;
uint32_t lastInputMs = 0;
uint32_t lastControlMs = 0;
uint32_t stepIndex = 0;
bool bleControllerConnected = false;
bool bleCommandConnected = false;
bram::ServoAction cachedPolicyAction{};
bool cachedPolicyActionValid = false;
int cachedPolicyPrimitiveKey = -1;

#if BRAM_ENABLE_BNO08X_POLICY_IMU
#ifndef D4
#define D4 6
#endif

#ifndef D5
#define D5 7
#endif

static constexpr int kPolicyImuSdaPin = D4;
static constexpr int kPolicyImuSclPin = D5;
static constexpr int kPolicyImuResetPin = -1;
static constexpr uint32_t kPolicyImuI2cHz = 400000;
static constexpr uint32_t kPolicyImuReportIntervalUs = 10000;

Adafruit_BNO08x policyBno08x(kPolicyImuResetPin);
sh2_SensorValue_t policySensorValue;
float latestPolicyQuat[4] = {1.0f, 0.0f, 0.0f, 0.0f};
bool policyImuReady = false;
bool policyImuHasQuat = false;

bool enablePolicyImuReports() {
  if (!policyBno08x.enableReport(SH2_ROTATION_VECTOR, kPolicyImuReportIntervalUs)) {
    Serial.println("Could not enable BNO08x rotation vector for policy");
    return false;
  }
  return true;
}

void setupPolicyImu() {
  Wire.begin(kPolicyImuSdaPin, kPolicyImuSclPin);
  Wire.setClock(kPolicyImuI2cHz);
  if (!policyBno08x.begin_I2C(BNO08x_I2CADDR_DEFAULT, &Wire) &&
      !policyBno08x.begin_I2C(0x4B, &Wire)) {
    Serial.println("BNO08x policy IMU not found; online policies will see identity quat");
    policyImuReady = false;
    return;
  }
  policyImuReady = enablePolicyImuReports();
  Serial.println(policyImuReady ? "BNO08x policy IMU ready" : "BNO08x policy IMU report setup failed");
}

void updatePolicyImu() {
  if (!policyImuReady) return;
  if (policyBno08x.wasReset()) {
    enablePolicyImuReports();
  }
  while (policyBno08x.getSensorEvent(&policySensorValue)) {
    if (policySensorValue.sensorId == SH2_ROTATION_VECTOR) {
      latestPolicyQuat[0] = policySensorValue.un.rotationVector.real;
      latestPolicyQuat[1] = policySensorValue.un.rotationVector.i;
      latestPolicyQuat[2] = policySensorValue.un.rotationVector.j;
      latestPolicyQuat[3] = policySensorValue.un.rotationVector.k;
      policyImuHasQuat = true;
    }
  }
}
#else
void setupPolicyImu() {}
void updatePolicyImu() {}
#endif

bool readPolicyImuQuaternion(float quatWxyz[4]) {
  updatePolicyImu();
#if BRAM_ENABLE_BNO08X_POLICY_IMU
  if (policyImuHasQuat) {
    for (int i = 0; i < 4; ++i) {
      quatWxyz[i] = latestPolicyQuat[i];
    }
    return true;
  }
#endif
  quatWxyz[0] = 1.0f;
  quatWxyz[1] = 0.0f;
  quatWxyz[2] = 0.0f;
  quatWxyz[3] = 0.0f;
  return false;
}

void setTargetCommand(float forward, float yaw, const char* source) {
  targetForward = clipFloat(forward, -1.0f, 1.0f);
  targetYaw = clipFloat(yaw, -1.0f, 1.0f);
  lastInputMs = millis();
  if (kPrintDebug) {
    Serial.printf("%s forward=%.3f yaw=%.3f\n", source, targetForward, targetYaw);
  }
}

#if BRAM_ENABLE_BLUEPAD32
ControllerPtr gamepads[BP32_MAX_GAMEPADS];

void onConnectedController(ControllerPtr ctl) {
  for (int i = 0; i < BP32_MAX_GAMEPADS; ++i) {
    if (gamepads[i] == nullptr) {
      gamepads[i] = ctl;
      if (kPrintDebug) {
        Serial.printf("Gamepad connected slot=%d\n", i);
      }
      bleControllerConnected = true;
      return;
    }
  }
  if (kPrintDebug) {
    Serial.println("Gamepad connected but no slot available");
  }
}

void onDisconnectedController(ControllerPtr ctl) {
  for (int i = 0; i < BP32_MAX_GAMEPADS; ++i) {
    if (gamepads[i] == ctl) {
      gamepads[i] = nullptr;
      if (kPrintDebug) {
        Serial.printf("Gamepad disconnected slot=%d\n", i);
      }
      targetForward = 0.0f;
      targetYaw = 0.0f;
      bleControllerConnected = false;
      return;
    }
  }
}
#endif

float clipFloat(float value, float low, float high) {
  if (value < low) return low;
  if (value > high) return high;
  return value;
}

float applyDeadband(float value) {
  value = clipFloat(value, -1.0f, 1.0f);
  if (fabsf(value) < kDeadband) return 0.0f;
  const float sign = value < 0.0f ? -1.0f : 1.0f;
  return sign * ((fabsf(value) - kDeadband) / (1.0f - kDeadband));
}

float slew(float current, float target) {
  const float delta = clipFloat(target - current, -kCommandSlewPerTick, kCommandSlewPerTick);
  return current + delta;
}

void selectPrimitiveCommand(float forward,
                            float yaw,
                            float& primitiveForward,
                            float& primitiveYaw) {
  primitiveForward = forward;
  primitiveYaw = yaw;
  const bool forwardActive = fabsf(forward) > 1.0e-3f;
  const bool yawActive = fabsf(yaw) > 1.0e-3f;
  if (!forwardActive || !yawActive || kBlendMixedCommands) {
    return;
  }
  if (kPrioritizeTranslationWhenMixed) {
    primitiveYaw = 0.0f;
  } else {
    primitiveForward = 0.0f;
  }
}

int primitiveKey(float forward, float yaw) {
  if (fabsf(forward) >= 0.05f) {
    return forward > 0.0f ? 1 : 2;
  }
  if (fabsf(yaw) >= 0.05f) {
    return yaw > 0.0f ? 3 : 4;
  }
  return 0;
}

int actionToPulseUs(float action, int servoIndex) {
  action = clipFloat(action, -1.0f, 1.0f);
  if (kServoInvert[servoIndex]) {
    action = -action;
  }
  const int neutral = kServoNeutralUs[servoIndex];
  if (action >= 0.0f) {
    return neutral + static_cast<int>((kServoMaxUs[servoIndex] - neutral) * action);
  }
  return neutral + static_cast<int>((neutral - kServoMinUs[servoIndex]) * action);
}

uint32_t pulseUsToDuty(int pulseUs) {
  static constexpr uint32_t maxDuty = (1UL << kPwmResolutionBits) - 1UL;
  static constexpr float periodUs = 1000000.0f / static_cast<float>(kPwmHz);
  return static_cast<uint32_t>(
      clipFloat((static_cast<float>(pulseUs) / periodUs) * maxDuty, 0.0f, maxDuty));
}

void attachServoPwm() {
  for (int i = 0; i < 3; ++i) {
#if defined(ESP_ARDUINO_VERSION_MAJOR) && ESP_ARDUINO_VERSION_MAJOR >= 3
    ledcAttach(kServoPins[i], kPwmHz, kPwmResolutionBits);
#else
    ledcSetup(kPwmChannels[i], kPwmHz, kPwmResolutionBits);
    ledcAttachPin(kServoPins[i], kPwmChannels[i]);
#endif
  }
}

void writeServoPulse(int servoIndex, int pulseUs) {
  const uint32_t duty = pulseUsToDuty(pulseUs);
#if defined(ESP_ARDUINO_VERSION_MAJOR) && ESP_ARDUINO_VERSION_MAJOR >= 3
  ledcWrite(kServoPins[servoIndex], duty);
#else
  ledcWrite(kPwmChannels[servoIndex], duty);
#endif
}

void writeServos(const bram::ServoAction& action) {
  for (int i = 0; i < 3; ++i) {
    writeServoPulse(i, actionToPulseUs(action.values[i], i));
  }
}

bool parseSerialCommand(const char* line, float& forward, float& yaw) {
  if (strcmp(line, "stop") == 0 || strcmp(line, "s") == 0) {
    forward = 0.0f;
    yaw = 0.0f;
    return true;
  }
  if (sscanf(line, "f %f y %f", &forward, &yaw) == 2) {
    return true;
  }
  if (sscanf(line, "%f %f", &forward, &yaw) == 2) {
    return true;
  }
  return false;
}

void handleCommandLine(const char* line, const char* source) {
  float forward = 0.0f;
  float yaw = 0.0f;
  if (parseSerialCommand(line, forward, yaw)) {
    setTargetCommand(forward, yaw, source);
  } else if (kPrintDebug) {
    Serial.printf("bad %s command: %s\n", source, line);
  }
}

void updateSerialInput() {
  static char line[80];
  static size_t length = 0;
  while (Serial.available() > 0) {
    const char c = static_cast<char>(Serial.read());
    if (c == '\n' || c == '\r') {
      if (length > 0) {
        line[length] = '\0';
        handleCommandLine(line, "serial");
      }
      length = 0;
    } else if (length + 1 < sizeof(line)) {
      line[length++] = c;
    }
  }
}

#if BRAM_ENABLE_BLUEPAD32
ControllerPtr activeGamepad() {
  for (int i = 0; i < BP32_MAX_GAMEPADS; ++i) {
    if (gamepads[i] && gamepads[i]->isConnected()) {
      return gamepads[i];
    }
  }
  return nullptr;
}

void updateBleInput() {
  BP32.update();
  ControllerPtr ctl = activeGamepad();
  if (!ctl) return;

  // Xbox-style mapping: left stick vertical = forward/back, right stick horizontal = yaw.
  const float forwardSign = kInvertGamepadForward ? -1.0f : 1.0f;
  const float yawSign = kInvertGamepadYaw ? -1.0f : 1.0f;
  const float forward =
      applyDeadband(forwardSign * static_cast<float>(ctl->axisY()) / kGamepadAxisScale);
  const float yaw =
      applyDeadband(yawSign * static_cast<float>(ctl->axisRX()) / kGamepadAxisScale);
  setTargetCommand(forward, yaw, "gamepad");

  if (ctl->b()) {
    setTargetCommand(0.0f, 0.0f, "gamepad");
  }
}
#endif

#if BRAM_ENABLE_BLE_COMMANDS
BLECharacteristic* bleTxCharacteristic = nullptr;

class BramBleServerCallbacks : public BLEServerCallbacks {
  void onConnect(BLEServer*) override {
    bleCommandConnected = true;
    if (kPrintDebug) {
      Serial.println("BLE command client connected");
    }
  }

  void onDisconnect(BLEServer* server) override {
    bleCommandConnected = false;
    setTargetCommand(0.0f, 0.0f, "ble");
    server->startAdvertising();
    if (kPrintDebug) {
      Serial.println("BLE command client disconnected; advertising restarted");
    }
  }
};

class BramBleRxCallbacks : public BLECharacteristicCallbacks {
  void onWrite(BLECharacteristic* characteristic) override {
    String value = characteristic->getValue();
    if (value.length() == 0) return;

    char line[80];
    const size_t count =
        value.length() < sizeof(line) - 1 ? value.length() : sizeof(line) - 1;
    memcpy(line, value.c_str(), count);
    line[count] = '\0';
    for (size_t i = 0; i < count; ++i) {
      if (line[i] == '\n' || line[i] == '\r') {
        line[i] = '\0';
        break;
      }
    }

    handleCommandLine(line, "ble");
    if (bleTxCharacteristic) {
      char reply[80];
      snprintf(reply, sizeof(reply), "f %.3f y %.3f\n", targetForward, targetYaw);
      bleTxCharacteristic->setValue(reply);
      bleTxCharacteristic->notify();
    }
  }
};

void setupBleCommands() {
  BLEDevice::init(kBleDeviceName);
  BLEServer* server = BLEDevice::createServer();
  server->setCallbacks(new BramBleServerCallbacks());

  BLEService* service = server->createService(kBleServiceUuid);
  BLECharacteristic* rxCharacteristic = service->createCharacteristic(
      kBleRxUuid, BLECharacteristic::PROPERTY_WRITE | BLECharacteristic::PROPERTY_WRITE_NR);
  bleTxCharacteristic = service->createCharacteristic(
      kBleTxUuid, BLECharacteristic::PROPERTY_READ | BLECharacteristic::PROPERTY_NOTIFY);

  rxCharacteristic->setCallbacks(new BramBleRxCallbacks());
  bleTxCharacteristic->addDescriptor(new BLE2902());
  bleTxCharacteristic->setValue("BRAM ready\n");

  service->start();
  BLEAdvertising* advertising = BLEDevice::getAdvertising();
  advertising->addServiceUUID(kBleServiceUuid);
  advertising->setScanResponse(true);
  BLEDevice::startAdvertising();
  Serial.println("Input mode: native BLE command service");
  Serial.println("BLE device name: BRAM");
}
#endif

void setupInput() {
  Serial.begin(115200);
  delay(250);
  Serial.println("Bram ESP32 controller boot");
  Serial.println("Serial command format: f 0.5 y -0.3   or: 0.5 -0.3   or: stop");

#if BRAM_ENABLE_BLUEPAD32
  if (!kUseSerialInput) {
    BP32.setup(&onConnectedController, &onDisconnectedController);
    Serial.println("Input mode: Bluepad32 BLE gamepad");
    if (kAllowSerialOverride) {
      Serial.println("Serial override enabled; send stop or f/y commands over USB.");
    }
  } else {
    Serial.println("Input mode: USB serial");
  }
#elif BRAM_ENABLE_BLE_COMMANDS
  if (!kUseSerialInput) {
    setupBleCommands();
    if (kAllowSerialOverride) {
      Serial.println("Serial override enabled; send stop or f/y commands over USB.");
    }
  } else {
    Serial.println("Input mode: USB serial");
  }
#else
  Serial.println("Bluepad32 disabled at compile time; serial input only");
#endif
}

void updateInput() {
  if (kUseSerialInput || kAllowSerialOverride) {
    updateSerialInput();
  }
  if (kUseSerialInput) return;
#if BRAM_ENABLE_BLUEPAD32
  updateBleInput();
#endif
}

void setup() {
  setupInput();
  setupPolicyImu();
  attachServoPwm();
  bram::ServoAction neutral{};
  writeServos(neutral);
  lastInputMs = millis();
  lastControlMs = millis();
}

void loop() {
  updateInput();

  const uint32_t now = millis();
  if (now - lastControlMs < kControlPeriodMs) {
    delay(1);
    return;
  }
  lastControlMs += kControlPeriodMs;

  if (now - lastInputMs > kInputTimeoutMs) {
    targetForward = 0.0f;
    targetYaw = 0.0f;
  }

  commandForward = slew(commandForward, targetForward);
  commandYaw = slew(commandYaw, targetYaw);

  float headingError = 0.0f;
  float yawRate = 0.0f;
  if (kUseImuCorrection) {
    // Fill this in once the 9DoF IMU driver is wired:
    // headingError = desired_heading - measured_heading;
    // yawRate = measured_gyro_z_rad_s;
  }

  float primitiveForward = 0.0f;
  float primitiveYaw = 0.0f;
  selectPrimitiveCommand(commandForward, commandYaw, primitiveForward, primitiveYaw);

  float policyQuat[4];
  readPolicyImuQuaternion(policyQuat);

  const bool yawOnly =
      fabsf(primitiveYaw) >= 0.05f && fabsf(primitiveForward) < 0.05f;
  const bool primitiveIdle =
      fabsf(primitiveYaw) < 0.05f && fabsf(primitiveForward) < 0.05f;
  const bool useBaseController =
      !kUseOnlinePolicies || (kUseBaseControllerForYaw && yawOnly);
  bram::ServoAction servoAction{};
  if (useBaseController) {
    servoAction = controller.action(primitiveForward, primitiveYaw, stepIndex, headingError, yawRate);
    cachedPolicyActionValid = false;
    cachedPolicyPrimitiveKey = -1;
  } else {
    const int key = primitiveKey(primitiveForward, primitiveYaw);
    const bool primitiveChanged = key != cachedPolicyPrimitiveKey;
    const bool updatePolicy =
        primitiveIdle || !cachedPolicyActionValid || primitiveChanged ||
        (stepIndex % kPolicyHoldTicks == 0);
    if (updatePolicy) {
      cachedPolicyAction = policyController.action(primitiveForward, primitiveYaw, policyQuat);
      cachedPolicyActionValid = true;
      cachedPolicyPrimitiveKey = key;
    }
    servoAction = cachedPolicyAction;
  }
  writeServos(servoAction);
  ++stepIndex;

  if (kPrintDebug && stepIndex % 40 == 0) {
    Serial.printf("cmd f=%.2f y=%.2f prim f=%.2f y=%.2f ble=%d action=[%.3f %.3f %.3f]\n",
                  commandForward,
                  commandYaw,
                  primitiveForward,
                  primitiveYaw,
                  (bleControllerConnected || bleCommandConnected) ? 1 : 0,
                  servoAction.values[0],
                  servoAction.values[1],
                  servoAction.values[2]);
  }
}

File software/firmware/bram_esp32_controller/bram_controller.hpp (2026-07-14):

#pragma once

#include <Arduino.h>
#include <cmath>
#include <cstddef>
#include <cstdint>

#include "bram_controller_data.hpp"

namespace bram {

struct ServoAction {
  float values[3];
};

struct ArcCommandView {
  const bram_data::ArcGridPoint* grid;
  std::size_t gridCount;
  bram_data::ArcParams fallback;
};

class BramController {
 public:
  ServoAction action(float forwardCommand,
                     float yawCommand,
                     std::uint32_t step,
                     float headingError = 0.0f,
                     float yawRate = 0.0f) const {
    const float forward = clip(forwardCommand, -1.0f, 1.0f);
    const float yaw = clip(yawCommand, -1.0f, 1.0f);
    const float forwardMag = std::fabs(forward);
    const float yawMag = std::fabs(yaw);
    const float t = static_cast<float>(step) * bram_data::kDt;

    if (forwardMag < 0.05f && yawMag < 0.05f) {
      return ServoAction{};
    }
    if (yawMag < 0.05f) {
      if (translationTableRows(forward) > 0) {
        return translationAction(forward, step);
      }
      float base[3];
      baseAction(forward, yaw, t, headingError, yawRate, base);
      return servoActionFromArray(base);
    }
    if (forwardMag < 0.05f) {
      return yawActionAtTime(yaw, t);
    }

    float base[3];
    baseAction(forward, yaw, t, headingError, yawRate, base);

    const float gate = residualGate(forward, yaw);
    if (gate <= 1.0e-6f) {
      return teacherAction(forward, yaw, step, base);
    }

    const ArcCommandView view = commandView(forward, yaw);
    const bram_data::ArcParams params =
        selectArcParams(view, std::fabs(forward), std::fabs(yaw));

    float yawActionValues[3];
    yawAction(yaw, static_cast<int64_t>(step) + params.stepOffset, yawActionValues);

    ServoAction out{};
    for (std::size_t i = 0; i < 3; ++i) {
      const float baseDelta = (params.baseScale - 1.0f) * base[i];
      const float rawResidual =
          (baseDelta + params.yawScales[i] * yawActionValues[i]) /
          maxFloat(1.0e-6f, bram_data::kResidualLimit * gate);
      const float residual = clip(rawResidual, -1.0f, 1.0f);
      out.values[i] = clip(base[i] + bram_data::kResidualLimit * gate * residual,
                           -1.0f,
                           1.0f);
    }
    return out;
  }

  ServoAction yawActionAtTime(float yawCommand, float elapsedSeconds) const {
    float yawValues[3];
    timedYawAction(yawCommand, elapsedSeconds, yawValues);
    return servoActionFromArray(yawValues);
  }

 private:
  static constexpr float kHeadingTrimLimit = 0.35f;

  static float clip(float value, float low, float high) {
    if (value < low) return low;
    if (value > high) return high;
    return value;
  }

  static float maxFloat(float a, float b) { return a > b ? a : b; }

  static float smoothstep(float x) {
    x = clip(x, 0.0f, 1.0f);
    return x * x * (3.0f - 2.0f * x);
  }

  static float residualGate(float forward, float yaw) {
    return smoothstep(std::fabs(forward) / 0.28f) *
           smoothstep(std::fabs(yaw) / 0.22f);
  }

  static void scaledParams(float forwardCommand, float yawCommand, float params[21]) {
    const float forward = forwardCommand;
    const float yaw = yawCommand;
    const float forwardMag = std::fabs(forward);
    const float yawMag = std::fabs(yaw);
    const float activity = clip(maxFloat(forwardMag, yawMag), 0.0f, 1.0f);
    const float* source = forward >= 0.0f ? bram_data::kForwardParams
                                          : bram_data::kBackwardParams;
    if (forwardMag < 0.05f && yawMag >= 0.05f) {
      source = bram_data::kForwardParams;
    }

    const float speedScale =
        activity < 0.05f
            ? 1.0f
            : bram_data::kBaseSpeedMin + (1.0f - bram_data::kBaseSpeedMin) * activity;
    const float actionScale =
        activity < 0.05f
            ? 0.0f
            : bram_data::kBaseActionMin + (1.0f - bram_data::kBaseActionMin) * activity;

    for (std::size_t i = 0; i < 21; ++i) {
      params[i] = source[i];
    }
    params[0] = source[0] * speedScale;
    for (std::size_t i = 1; i < 4; ++i) params[i] = source[i] * actionScale;
    for (std::size_t i = 4; i < 7; ++i) params[i] = source[i] * actionScale;
    for (std::size_t i = 10; i < 13; ++i) params[i] = source[i] * actionScale;
  }

  static void gaitAction(const float params[21],
                         float t,
                         float headingError,
                         float yawRate,
                         bool useHeadingCorrection,
                         float out[3]) {
    const float thetaBase = 2.0f * PI * params[0] * t;
    for (std::size_t i = 0; i < 3; ++i) {
      const float theta = thetaBase + params[7 + i];
      out[i] = params[1 + i] + params[4 + i] * std::sin(theta) +
               params[10 + i] * std::sin(2.0f * theta + params[18 + i]);
    }

    if (useHeadingCorrection) {
      float trim = -params[13] * headingError - params[14] * yawRate;
      trim = clip(trim, -kHeadingTrimLimit, kHeadingTrimLimit);
      for (std::size_t i = 0; i < 3; ++i) {
        out[i] += trim * params[15 + i];
      }
    }

    for (std::size_t i = 0; i < 3; ++i) {
      out[i] = clip(out[i], -1.0f, 1.0f);
    }
  }

  static void baseAction(float forwardCommand,
                         float yawCommand,
                         float t,
                         float headingError,
                         float yawRate,
                         float out[3]) {
    float params[21];
    scaledParams(forwardCommand, yawCommand, params);
    const bool useHeadingCorrection =
        std::fabs(forwardCommand) >= 0.05f && std::fabs(yawCommand) < 0.05f;
    gaitAction(params, t, headingError, yawRate, useHeadingCorrection, out);
  }

  static int positiveMod(int64_t value, int mod) {
    int result = static_cast<int>(value % mod);
    return result < 0 ? result + mod : result;
  }

  static ServoAction servoActionFromArray(const float values[3]) {
    ServoAction out{};
    for (std::size_t i = 0; i < 3; ++i) {
      out.values[i] = clip(values[i], -1.0f, 1.0f);
    }
    return out;
  }

  static ServoAction translationAction(float forwardCommand, std::uint32_t step) {
    const float magnitude = std::fabs(forwardCommand);
    ServoAction out{};
    if (magnitude < 1.0e-6f) {
      return out;
    }
    const bool forward = forwardCommand > 0.0f;
    const std::size_t rows =
        forward ? bram_data::kForwardTableRows : bram_data::kBackwardTableRows;
    const int row = positiveMod(step, static_cast<int>(rows));
    for (std::size_t i = 0; i < 3; ++i) {
      const float value = forward ? bram_data::kForwardTable[row][i]
                                  : bram_data::kBackwardTable[row][i];
      out.values[i] = clip(magnitude * value, -1.0f, 1.0f);
    }
    return out;
  }
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

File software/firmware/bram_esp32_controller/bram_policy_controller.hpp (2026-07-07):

#pragma once

#include <Arduino.h>
#include <cmath>
#include <cstddef>

#include "bram_controller.hpp"
#include "bram_policy_data.hpp"

namespace bram {

class BramPolicyController {
 public:
  static constexpr std::size_t kYawPolicyHoldTicks = 2;

  BramPolicyController() {
    const float identityQuat[4] = {1.0f, 0.0f, 0.0f, 0.0f};
    reset(identityQuat);
  }

  void reset(const float quatWxyz[4]) {
    float normalized[4];
    normalizeQuat(quatWxyz, normalized);
    fillHistories(normalized);
    activePrimitive_ = Primitive::Idle;
    yawHoldTicksRemaining_ = 0;
    cachedAction_ = ServoAction{};
  }

  ServoAction action(float forwardCommand, float yawCommand, const float quatWxyz[4]) {
    const float forward = clip(forwardCommand, -1.0f, 1.0f);
    const float yaw = clip(yawCommand, -1.0f, 1.0f);
    const Primitive primitive = selectPrimitive(forward, yaw);

    float quat[4];
    normalizeQuat(quatWxyz, quat);

    if (primitive == Primitive::Idle) {
      reset(quat);
      return ServoAction{};
    }

    if (primitive != activePrimitive_) {
      fillHistories(quat);
      activePrimitive_ = primitive;
      yawHoldTicksRemaining_ = 0;
    } else if (primitive == Primitive::Yaw && yawHoldTicksRemaining_ > 0) {
      --yawHoldTicksRemaining_;
      return cachedAction_;
    } else {
      pushImu(quat);
    }

    const float commandScalar = primitive == Primitive::Yaw ? yaw : 0.0f;
    float obs[bram_policy_data::kObsDim];
    buildObservation(commandScalar, obs);

    float output[bram_policy_data::kActionDim];
    infer(weightsFor(primitive), obs, output);

    const float scale =
        primitive == Primitive::Forward || primitive == Primitive::Backward
            ? std::fabs(forward)
            : 1.0f;

    ServoAction out{};
    for (std::size_t i = 0; i < bram_policy_data::kServoCount; ++i) {
      out.values[i] = clip(scale * output[i], -1.0f, 1.0f);
    }
    pushAction(out.values);
    cachedAction_ = out;
    yawHoldTicksRemaining_ =
        primitive == Primitive::Yaw ? kYawPolicyHoldTicks - 1 : 0;
    return out;
  }

 private:
  enum class Primitive {
    Idle,
    Forward,
    Backward,
    Yaw,
  };

  Primitive activePrimitive_ = Primitive::Idle;
  std::size_t yawHoldTicksRemaining_ = 0;
  ServoAction cachedAction_{};
  float imuHistory_[bram_policy_data::kImuHistoryFrames][bram_policy_data::kImuFrameDim]{};
  float actionHistory_[bram_policy_data::kActionHistoryFrames][bram_policy_data::kServoCount]{};

  static float clip(float value, float low, float high) {
    if (value < low) return low;
    if (value > high) return high;
    return value;
  }

  static Primitive selectPrimitive(float forward, float yaw) {
    if (std::fabs(forward) >= 0.05f) {
      return forward > 0.0f ? Primitive::Forward : Primitive::Backward;
    }
    if (std::fabs(yaw) >= 0.05f) {
      return Primitive::Yaw;
    }
    return Primitive::Idle;
  }

  static const bram_policy_data::ActorWeights& weightsFor(Primitive primitive) {
    switch (primitive) {
      case Primitive::Forward:
        return bram_policy_data::kForwardPolicy;
      case Primitive::Backward:
        return bram_policy_data::kBackwardPolicy;
      case Primitive::Yaw:
        return bram_policy_data::kYawPolicy;
      case Primitive::Idle:
      default:
        return bram_policy_data::kForwardPolicy;
    }
  }

  static void normalizeQuat(const float in[4], float out[4]) {
    float norm = std::sqrt(
        in[0] * in[0] + in[1] * in[1] + in[2] * in[2] + in[3] * in[3]);
    if (!(norm > 1.0e-6f)) {
      norm = 1.0f;
      out[0] = 1.0f;
      out[1] = out[2] = out[3] = 0.0f;
      return;
    }
    const float invNorm = 1.0f / norm;
    for (std::size_t i = 0; i < 4; ++i) {
      out[i] = in[i] * invNorm;
    }
  }

  void fillHistories(const float quat[4]) {
    for (std::size_t frame = 0; frame < bram_policy_data::kImuHistoryFrames; ++frame) {
      for (std::size_t axis = 0; axis < bram_policy_data::kImuFrameDim; ++axis) {
        imuHistory_[frame][axis] = quat[axis];
      }
    }
    for (std::size_t frame = 0; frame < bram_policy_data::kActionHistoryFrames; ++frame) {
      for (std::size_t servo = 0; servo < bram_policy_data::kServoCount; ++servo) {
        actionHistory_[frame][servo] = 0.0f;
      }
    }
  }

  void pushImu(const float quat[4]) {
    for (std::size_t frame = 0; frame + 1 < bram_policy_data::kImuHistoryFrames; ++frame) {
      for (std::size_t axis = 0; axis < bram_policy_data::kImuFrameDim; ++axis) {
        imuHistory_[frame][axis] = imuHistory_[frame + 1][axis];
      }
    }
    for (std::size_t axis = 0; axis < bram_policy_data::kImuFrameDim; ++axis) {
      imuHistory_[bram_policy_data::kImuHistoryFrames - 1][axis] = quat[axis];
    }
  }

  void pushAction(const float action[3]) {
    for (std::size_t frame = 0; frame + 1 < bram_policy_data::kActionHistoryFrames; ++frame) {
      for (std::size_t servo = 0; servo < bram_policy_data::kServoCount; ++servo) {
        actionHistory_[frame][servo] = actionHistory_[frame + 1][servo];
      }
    }
    for (std::size_t servo = 0; servo < bram_policy_data::kServoCount; ++servo) {
      actionHistory_[bram_policy_data::kActionHistoryFrames - 1][servo] =
          clip(action[servo], -1.0f, 1.0f);
    }
  }

  void buildObservation(float commandScalar, float obs[bram_policy_data::kObsDim]) const {
    std::size_t index = 0;
    for (std::size_t frame = 0; frame < bram_policy_data::kImuHistoryFrames; ++frame) {
      for (std::size_t axis = 0; axis < bram_policy_data::kImuFrameDim; ++axis) {
        obs[index++] = imuHistory_[frame][axis];
      }
    }
    for (std::size_t frame = 0; frame < bram_policy_data::kActionHistoryFrames; ++frame) {
      for (std::size_t servo = 0; servo < bram_policy_data::kServoCount; ++servo) {
        obs[index++] = actionHistory_[frame][servo];
      }
    }
    obs[index++] = clip(commandScalar, -1.0f, 1.0f);
  }

  static void infer(const bram_policy_data::ActorWeights& weights,
                    const float obs[bram_policy_data::kObsDim],
                    float out[bram_policy_data::kActionDim]) {
    float h0[bram_policy_data::kHiddenDim];
    float h1[bram_policy_data::kHiddenDim];

    for (std::size_t row = 0; row < bram_policy_data::kHiddenDim; ++row) {
      float sum = weights.b0[row];
      for (std::size_t col = 0; col < bram_policy_data::kObsDim; ++col) {
        sum += weights.w0[row][col] * obs[col];
      }
      h0[row] = std::tanh(sum);
    }

    for (std::size_t row = 0; row < bram_policy_data::kHiddenDim; ++row) {
      float sum = weights.b1[row];
      for (std::size_t col = 0; col < bram_policy_data::kHiddenDim; ++col) {
        sum += weights.w1[row][col] * h0[col];
      }
      h1[row] = std::tanh(sum);
    }
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

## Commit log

2026-06-30 built out mujoco model + intial testing of "can it walk"
    [15cm_leg.obj, 17cm_leg.obj, battery.obj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]
2026-06-30 new tuff env, changes and approaches taken over this night outlined in journal yaw and wtuff for tmr yawn im sleepy
